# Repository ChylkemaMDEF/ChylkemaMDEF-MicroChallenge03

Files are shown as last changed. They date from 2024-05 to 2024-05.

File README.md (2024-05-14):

# MicroChallenge03 _Carlotta Hylkema & Oliver Lloyd

The third and final microchallenge that took place during our Masters in Design for Emergent Futures at IAAC and ELISAVA in Barcelona. This project was done by Oliver Lloyd and Carlotta Hylkema, as a continuation of our thesis project fociussing on energy usage and finding ways to decrease our consumption not only in homes but also in other systems. This challenge however focussed more on the final design echibition that takes place on June 10th. The technical development of our project took place more during the second microchallenge which can be found here [MicoChallenge 02](https://github.com/ChylkemaMDEF/MicroChallenge-2-Energy-Bot). If you want to view our personal MDEF sites you can find them here:

* [Carlotta's Site](https://chylkemamdef.github.io/MyPortfolio/index.html)
* [Oliver's Site](https://oliver-lloyd-mdef.github.io/Oliver-MDEF-Portfolio/)

# The Goal of this Challenge

We were unsure of the way we wanted to approach this microchallenge at first as the original brief about taking input from the body and translating this into some form of data was not directly linked to our proejct. However, once we started the class Santi made a point tha twe could sue this in more of the side of Exhibit Design and Interaction of the people visiting our journey. We brainstormed of ways we could gather input from the people and which potential output we could generate based on this. In the end we decided to create a interaction at the start of our display that creates a sense of impact and interaction into the problem of energy.

Brainstorm

**_Inspiration Projects_**:
* [Energy Grid Project](https://www.most.org/explore/energy-powering-our-future/)
* [Future Starts Here](https://www.dezeen.com/2018/05/11/vas-the-future-starts-here-exhibition-explores-dark-and-bright-sides-of-tomorrow/)
* [Happy Joy Stick](https://fablabbcn.org/blog/theclass/controlling-real-life-objects-with-a-joystick)

From this brainstorming session we defined the following:

The defined input is: **A dial in which people have the power to determine the amount of energy being released based on what averages of other countries is**

The defined output is: **A group of household electronic machines that start turning on in relation to the energy budget set as the input. All of these things will create an overwhelming feeling of input and things like a tv or radio will give feedback based on the energy problem to the person at the dial**

The defined interaction is: **A way for people to interact with what energy entails and how in modern society we use energy. The interaction should be physical and make use of various senses like hearing, touch, sight.**

# The Plan
Before we started with this challenge we discussed the steps we felt needed to reach the end goal, and which skills and things were needed beforehand. We wanted to work mostly on hardware during this challenge and get as much done for the display part of MDEFFest so that in the coming weeks we can focus more on further device and AI development. This is why this week was more focussed on the display, however as we didn't want to lose to much momentum we also scheduled moments to work on the AI infrastructure and PCB development for the physical devices of our design project. This was the original planning we had made and we focussed on these primary steps before adding anything else to keep us on track:



There was a division of tasks that took place throughout the week but in all aspects we helped eachother in the design. Carlotta took the lead in the creation of the arduino code and the electrical relay box. Oliver on the other hand spent the first day trying to better understand how we could create the physical display stand. After the first days of creating these seperate parts we came together to test the electrical box and finish building the setup. We both worked on the posters that were displayed, Carlotta on the dial poster and Oliver on the table poster.  Also in tandem to the work we show in this repo, we were working on further development of our AI bot so we both spent some time trying to build the PCB (Oliver) and better understanding the functions of our AI (Carlotta).

# The Process

https://github.com/ChylkemaMDEF/ChylkemaMDEF-MicroChallenge03/assets/147051108/04fdbdea-2375-44fe-941d-bf933d1b6775

## Building the Relay Circuit and Power Box
The circuit of this device was quite simple as it required a translation of a rotation of a dial into certain devices being turned on or off gradually. We brainstormed about different potential ways this could happen and it was determined that the best way was to use a potentiometer and several relays that are each connected to their own individual plug.The wanted interaction is as followed:

WhatsApp Image 2024-05-07 at 16 17 45_5aa18951

From here we researched online how we could connect a single outlet in the wall to multiple plugs and relays. Some of the most helpful diagrams and articles that we used were:

* [Turning an appliance into a smart device](https://www.circuitbasics.com/build-an-arduino-controlled-power-outlet/)
* [Splitting Power with Multiple Relays](https://electronics.stackexchange.com/questions/205286/splitting-mains-power-into-multiple-relay-switched-circuits)
* [Controlling multiple outlets with SSR Relay](https://forum.arduino.cc/t/controlling-multiple-outlets-with-ssr-relay-module-and-arduino/1218455)

When looking at the interaction we wanted and the way we wanted the device to fucntion we created a flowchart for the arduino code needed.

Energy Relationships - Function Arduino Code

### The Physical Ciruit
Now that we had a better idea of what we wanted to build we ended up talking to Aurel about our idea and he suprised us by telling us that he had done a similar project for the electrical box and could share his knowledge with us. This helped a lot as from him we received the 3D file to print the box to store all the electrical components. From here we took a look at his created box and then made a design for how each wires would need to be connected to each other. The original idea for a connection of wires is shown in the following picture. We decided as this was for personal use to forgo the ground wire and instead plug the end into an extension plug as the safety. 

DiagramCircuitMicroChallenge03

#### Bill of Materials Circuit Dial (For 4 plug device)
* 1x Breadboard
* 1x Barduino or Arduino board 
* 2x 2 Channel DC 5V Relay Module-Low Level Trigger
* Multiple Thick 240V Wires
* 2x 4 to 1 Lever Wire Connectors
* 2x 2 to 1 Lever Wire Connectors
* 4x Sockets
* 1x Wire with Wall Plug
* 1x Potentio Meter
* 1x Casing 3D Printed

#### The steps to follow:
1. 3D print casing for electrical components
2. Screw 2 240V wires into each relay, check your relay first to see which of the two outer connectors you need. For us it was center and right connections. By screwing these in first you then have an easier job ahead. We did this once the relay was screwed in and it was much more difficult.
3. Screw relays into box
4. Now you need to follow the diagram shown above to connect the plug wires together.
   
   4.1 The live wire (blue usually) from the wall plug needs to go into one of the 4 to 1 connectors. Then 1 wire from each relay attaches to this connector as well.
   
   4.2 The other wire from each relay will attach to the individual plugs. On the back of the plug you can see a L and an N. The wires from the relay attach to the L.
   
   4.3 Then you need to attach a wire to each N port of the plug into a new 4 to 1 connectors. The last port of this connector will be the neutral wire (usually brown) from the wall plug.
   
   4.4 Now double check if all connections are correct and stuck.
5. Now the final step is to connect the relays to the Arduino board.

   5.1 Connect 4 wires to each relay
   
   5.2 Connect the voltage wires of the relay to the 5V ground input of the arduino. If it is 3.3V or 5V depends on the relay so be sure to check this
   
   5.3 Connect the ground wires of the ground of the arduino.
   
   5.4 Connect all the pin wires of each relay to the digital pins of the arduino board. Make sure to take note of which relay pin is connected to which plug. You can always test this after but it makes it easier        to take note beforehand.

6. Connect Arduino to powersource (we used a powerbank) and run the code. When testing be sure to plug into a extension cord with ground and have this switched off when plugging devices into the created box. This    ensures maximum safety while testing.

### The Code Needed
The code we used for this project is very easy simple as can be seen in the flowchart above. It was important for us that it was adaptable to multiple relays incase we wanted to add more plugs in the end. The box I explained above was for 4 plugs but in the end we connected another box to ours to get 6 workable outputs in the end. The code is explained below in detail.

First you need to setup the code to handle the different variables and set the maximum angle of the potentiometer:

      #define ROTARY_ANGLE_SENSOR 1
      #define ADC_REF 5
      #define GROVE_VCC 5
      #define FULL_ANGLE 300
      
      #define NUM_RELAYS  6 // Change this number based on how many relays you have
      int relayPins[NUM_RELAYS] = {5,6,8,10,12,13}; // Store the pins for the relay in an array this allows them to be called dynamically
      int increments = FULL_ANGLE /NUM_RELAYS ;

Then it is time to setup the pinmodes and the most important part to set the relays to off so that when the code starts there is no energy flowing through the plugs and all the devices start turned off when the dial is at 0 degrees:

      pinMode(ROTARY_ANGLE_SENSOR, INPUT); // set pinmode of dial
      
      digitalWrite(relayPins[6], LOW);
    
      // set pinmode and state of each relay dynamically
      for (int i = 0; i < NUM_RELAYS; i++) {
        pinMode(relayPins[i], OUTPUT);
        digitalWrite(relayPins[i], LOW);
      }
      }

Within the loop you call for the degrees, that are used to determine how many relays will be turned on, by using a created function called Getdegrees. This function reads the data from the potentiometer and send it back to the looped code:

      int getDegree() {
        int sensor_value = analogRead(ROTARY_ANGLE_SENSOR);
        float voltage = (float)sensor_value * ADC_REF / 4095;
        float degrees = (voltage * FULL_ANGLE) / GROVE_VCC;
        return degrees;
        }

In the main loop there are 2 main parts, the code that runs if the angle is 0 degrees and then the code that is done for if it is above this. The first step for the loop is to determine how many relays should turn on. If the dial is set to 0 then all the relays will be switched to 0 using an iterative loop to make sure all the relays that were potentially on before are now turned off(LOW):

      if (degrees == 0){
          for (int i = 0; i < NUM_RELAYS; i++){ // by setting i to 0 it needs to be less then as array stores from 0 to ..
            digitalWrite(relayPins[i], LOW);
            Serial.print("Relays Off");
          }

The last important function in the code is the code that checks what the degrees are and the amount of relays to turn on. This is done by checking the amount of relays set at the beginning and the total degrees of the full potentiometer. By this increments are determined. Then when the degrees are read and above 0. The read degrees is divided by the incremenets to see how many relays are turned on (HIGH):
      
      if (degrees > 0) {
          int activeRelays = degrees / increments; 
          
          // Loop through i being the amount of relays to turn on, and then for each relay turn this on. So it activeRelays = 2 it goes through twice and turns on relay1 + relay 2
          for (int i = 0; i <= activeRelays && i < NUM_RELAYS; i++) {
            digitalWrite(relayPins[i], HIGH);
            Serial.print("Activating relay ");
            digitalWrite(relayPins[i+1], LOW);
            Serial.println(i + 1);
      
          }
        }

### Building the Dial Setup 

The final part of the challenge was focussed on building the stand for the dial and determining the infographics that we wanted to display to the people. This was actually a fun process in which we designed a box in Fusion360 and then used a lasercutter to cut the individual parts and then putting the box together using hot glue and latches. 

####  Bill of Materials Stand Display

* Lasercutter
* Hot Glue
* Clamps
* 2x 1.3 m by .9 m plywood (3 - 4 mm thick) (this area of woood can be changed depending on the size of the layercutter)
* 3d printed knob

In the process of building this dial it was quite simple. We started by making a quick mockup in Fusion360 and using AR software to get a feeling for size. We then focussed on making a paper prototype to see if the shape was truly what we like. We ran across the problem that are original idea was way to large for the actual printer. We scaled it down and cut at an angle but of course the grain was off so there was too much tension on the dial. In the end we altered our design to be a smaller dial case of 30cm diamter that was sat on a larger table. 

#### The Steps to Create the Setup:

1. Model the design in a 3D CAD software
2. Create 2D designs that can be used for the lasercutter
3. Lasercut all the pieces
4. Prepare the knob file for the 3D printer
5. Put the knob onto the printer
6. Once all parts are prepare it is time to assemble. Use the hotglue to attach the wrap around part of the design to the top plate of the dial case.
7. In the mean time build the round table by slotting the two cross parts together and slotting into the cuts on the tabletop. At this time you can add any inforgraphic you might want.
8. Once the glue is dried attach the potentiometer to the top using small screws, add the infographic if desired and attach the printed knob.
9. Take wires from the energy box and lead up to the dial and attach the arduino and powerbank to the potentiometer

## The Outcome

### Created Energy Box
In the end we ended up with an energy box connected to a second box that was able to work based on the angle of the dial on the setup. Based on the degrees the relays would turn on and as the angle went up more and more relays turned on. This allowed for us to control the output based on the dial the person was turning. Effectively taking the inputted movement of the person and outputting electrical current to devices connected. This in turn created a feeling of having the power to power the world.

energyboc

### Display Dial Working and Turning on Devices
The actual final display of the week was the dial setup and having classmates interact with it. The goal of this was to combine the code, electrical box and physical stand to create an experience in which the urgency of the energy issue is shown and people start to engage and think about what this is. There are still a few things we want to changem like the top poster we want to lasercut into the top plate so that it has a bit more of a clean feature. We also need to spend some more time considering what actual outputs we would like and how these could grow based on the amount of relays turned on.

https://github.com/ChylkemaMDEF/ChylkemaMDEF-MicroChallenge03/assets/147051108/75f3b5a2-39b5-4ea5-ab6a-dfa4f91619cd

WhatsApp Image 2024-05-13 at 17 01 46_ba902437

## Reflecting and Moving Forward

For this challenge we were happy to focus on a bit more hardware and physical interaction design, as the rest of our project really relies on people interacting with software based tools it was a nice change of pace. It also really got us thinking about the MDEF fest (the final showcase at the end of the year where we exhibit the research we've been working on) and how we were going to get people to interact with our display stand and understand the research we'd been working on. 

It was nice to see that a relatively simple idea of a large dial that invited you to turn on the power to the world became so effective at illustrating the point of energy overconsumption. The entire idea behind our research is not to make individuals feel as though it is their fault that we are consuming so much, rather it is to galvanise them to reflect and want to take action, no matter how small. Watching members of our class interact with the dial and rad the information displayed, it was great to see that this was actually giving them pause and take a moment to understand exactly what the numbers of consumption meant. To that end it was really good to have the various appliances plugged in to create a form of overwhelming sensory experience to try and illustrate that. 
We recieved some really good feedback from that first showing and we are looking forward to implementing that into the final display. 

The order in which the appliances are turned on is going to be very important, we are going to have to restructure it in such a way that the most essential appliances turn on first and scale to up to more and more convenience or luxury items that aren't strictly necessary to survival but to a quality of life that we've become accustomed to. That's going to be really important because if we can illustrate that the items that we deem "essential" aren't necessarily so but we feel like we couldn't live without them, then perhaps that would be enough to motivate people to stop and reflect on just how much energy they use and is embodied in them, and if there was a better way to keep using those conveniences but with a lower energy consumption bill. 

That would be great, and is going to be the next step that we are going to focus on for the exhibit design of The WattWise Project.

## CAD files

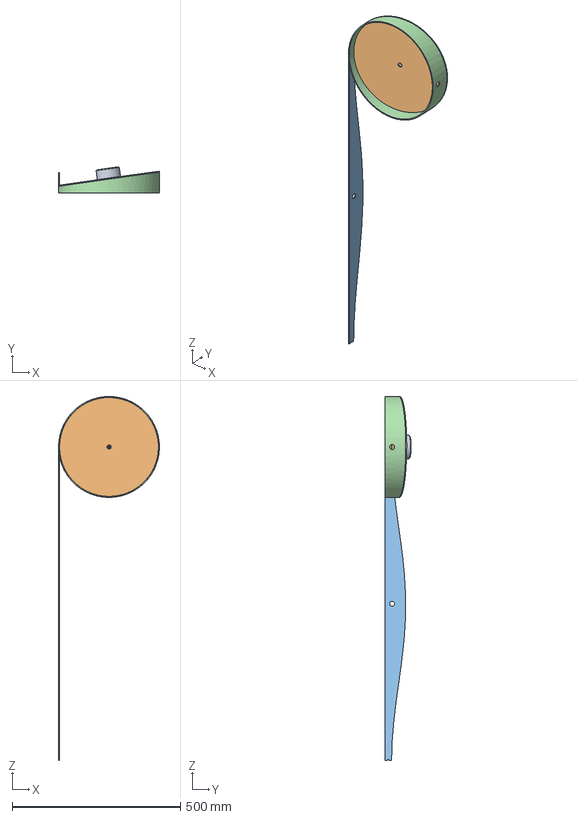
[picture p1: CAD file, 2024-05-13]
DisplayStand/Exhibit Dial Stand v12.step
300.0 x 78.3 x 1081.8 mm
Dial
Dial Stand Top Plate
Dial stand Back Wrap with Tabs

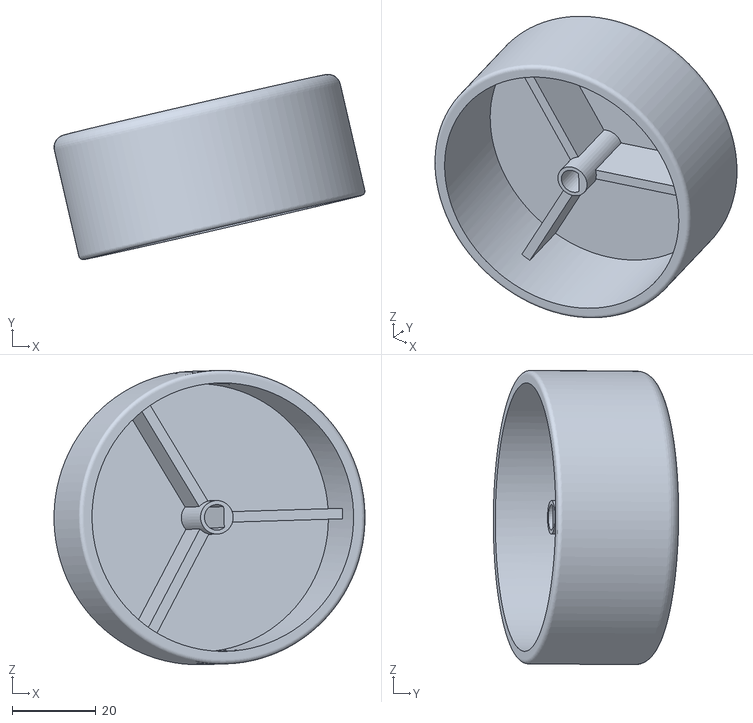
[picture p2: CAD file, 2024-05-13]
DisplayStand/Exhibit Dial Stand_Dial v2.stl
74.1 x 44.2 x 70.2

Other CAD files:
ElectricalBox/Rugged Relay Box Parametric_Microchallenge 03_MDEF v3.f3d

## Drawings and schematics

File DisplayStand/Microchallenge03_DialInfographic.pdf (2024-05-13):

# SPAIN Uruguay

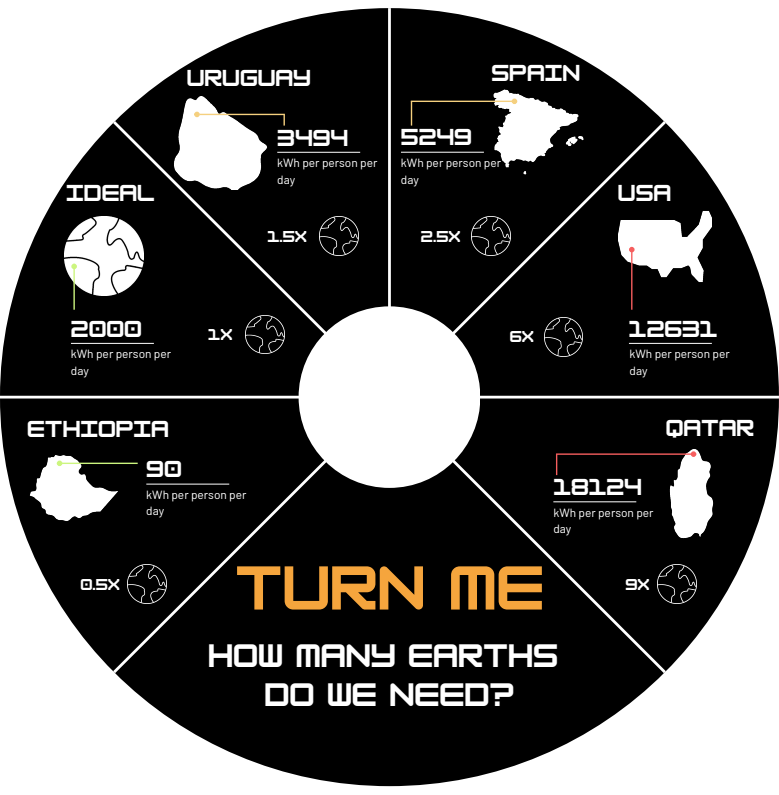
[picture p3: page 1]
TURN ME; USA; Ethiopia; Qatar; idEAL; kWh per person per; day

kWh per person per
day

How many earths
do we need?

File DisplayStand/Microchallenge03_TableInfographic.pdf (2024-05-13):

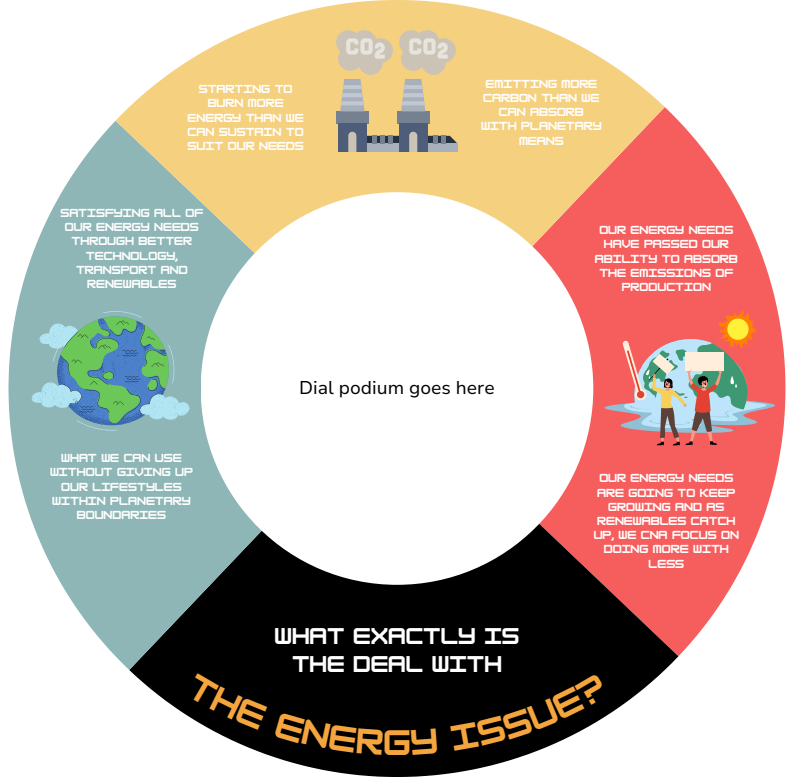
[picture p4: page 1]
means; less

Emitting more
carbon than we
can absorb
with planetary

Starting to
burn more
energy than we
can sustain to
suit our needs

Satisfying all of
our energy needs
through better
technology,
transport and
renewables

Our energy needs
have passed our
ability to absorb
the emissions of
production

Dial podium goes here

What we can use
without giving up
our lifestyles
within planetary
boundaries

Our Energy needs
are going to keep
growing and as
renewables catch
up, we cna focus on
doing more with

What exactly is
the deal with

The energy issue?
